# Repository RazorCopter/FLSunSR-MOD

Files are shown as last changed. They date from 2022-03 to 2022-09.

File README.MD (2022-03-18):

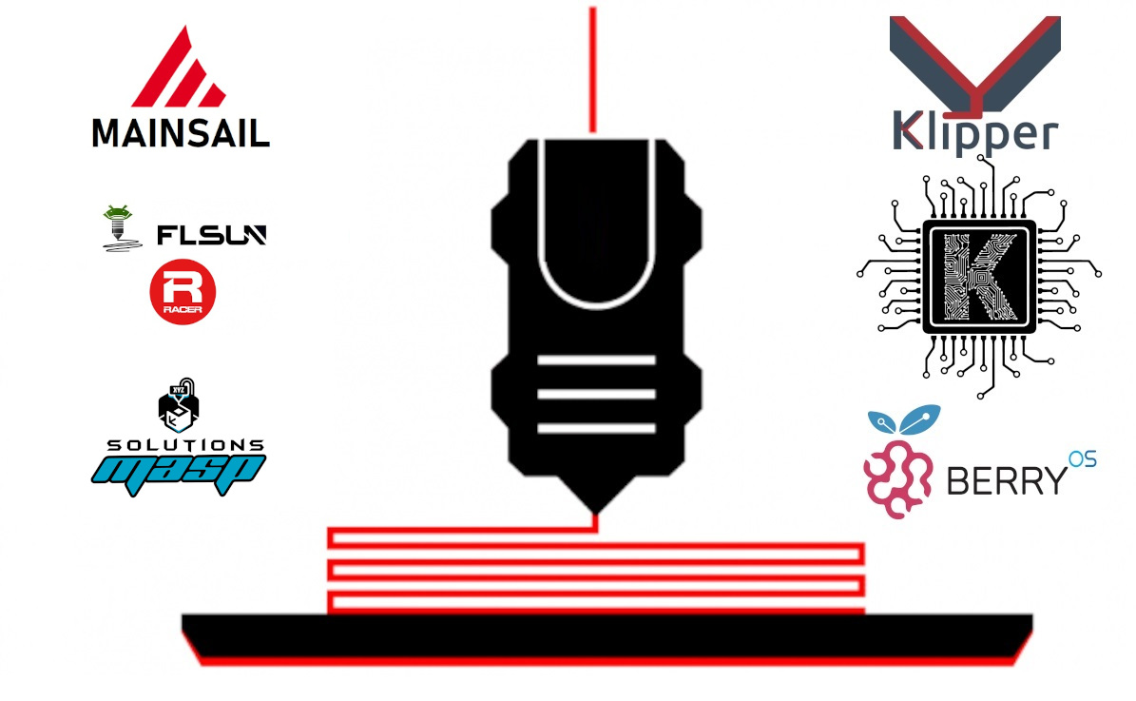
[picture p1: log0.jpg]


# Klipper + MAINSAIL >> FLSUN_SR

################### HW MOD ####################
+ Raspberry Pi 3B+
+ MASP HEAT BREAK [CTCore®] + VOLCANO
+ 2X NOCTUA FAN
+ DUALDRIVE BONDTECH EXTRUDER
+ LED-STRIP IN TOWERS 2835 24V
+ DISPLAY IPS 4.3" TOUCH CAPACITIVE
+ HOUSING & FAN DUCT REDESIGNED
+ CAM FULLHD

################### SW MOD #####################
- Klipper v0.10.x
- MainSail  v2.1.2
- Moonraker v0.7.1-x
- KlipperScreen v0.2.x

##################   Optional by KIAUH   #################

URL: https://github.com/th33xitus/kiauh

###############################################

# Install Klipper FLSUN SR:

 PREREQUISITES:
> Raspberry 
> Optional Display 
> Elettrical connection:
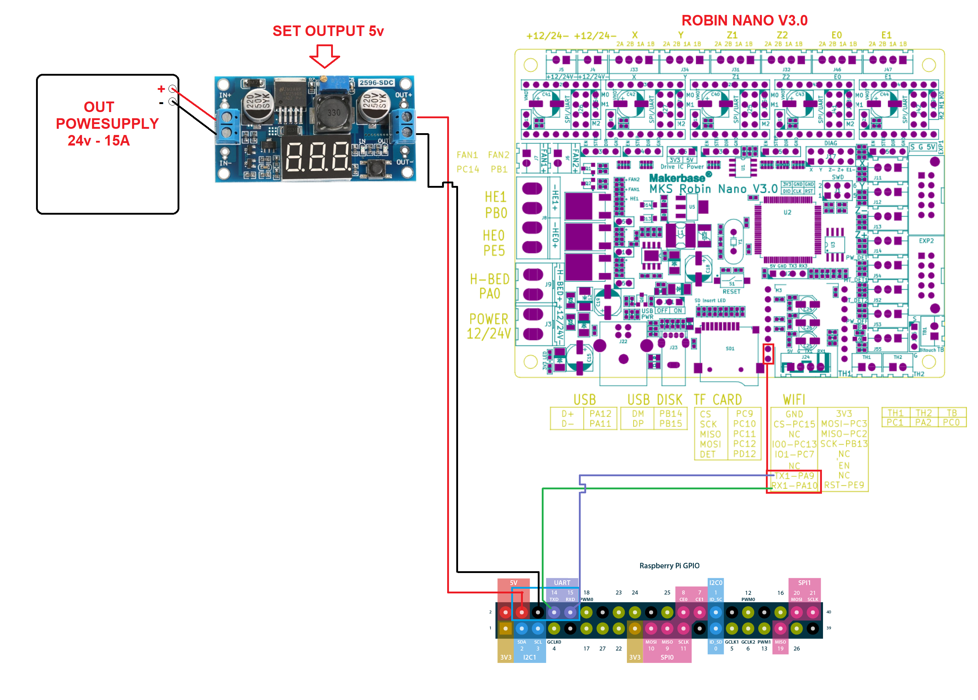
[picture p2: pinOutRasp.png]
PinLink


# STEP 1:
- Install Mainsail OS 
-     > https://github.com/mainsail-crew/MainsailOS/releases
-     > Guide: https://3dprintbeginner.com/how-to-install-mainsailos-on-raspberry-pi/

# STEP 2:
- SSH IP Raspberry (User/pwd > pi/raspberry)
- Launch commands:
```
cd klipper
make menuconfig
```
- ############################### SETTINGS ##############################
```
      > Micro-controller Architecture (STMicroelectronics STM32)  --->
      > Processor model (STM32F407)  --->
      > Bootloader offset (48KiB bootloader (MKS Robin Nano V3))  --->
      > Clock Reference (8 MHz crystal)  --->
      > Communication interface (Serial (on USART1 PA10/PA9))  --->
      > (250000) Baud rate for serial port
```
- Q > Yes
- Command: 
```
make
```
- copy generate file: /home/pi/klipper/out/klipper.bin in new SDCARD and rename in: Robin_nano_v3 (you can find it among the files here]

# STEP 3:
- Insert sdcard in the nano robin and wait and power-on SR
- Restart SR

# STEP 4:
- Open mainsail from browser
- leftmenu > Machine > edit printer.cfg :
```
[mcu]
serial: /dev/ttyAMA0
restart_method: command
baud: 250000
```
  
# NOTE:
- Serial port check: open ssh raspberry e launch command: 
```
ls /dev/ttyAMA*
```

//==========================================================================
//==========================================================================
//==========================================================================

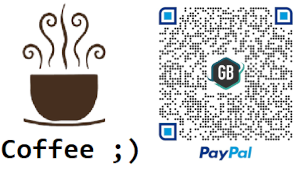
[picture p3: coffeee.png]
coffeee


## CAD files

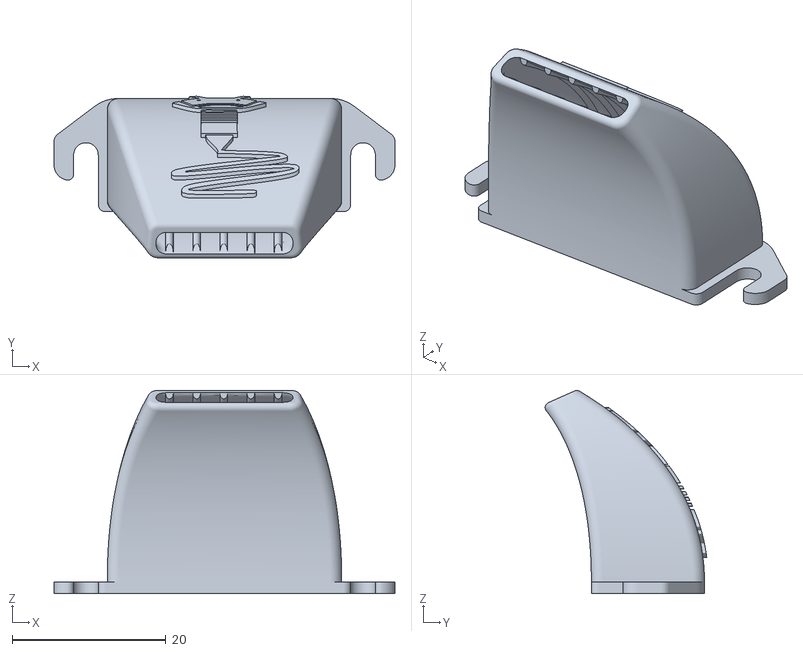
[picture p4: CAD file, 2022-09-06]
STL SR/FLSUN SR Fan_Duct V3 Fast Mount with logo.stl
44.3 x 21.0 x 26.4

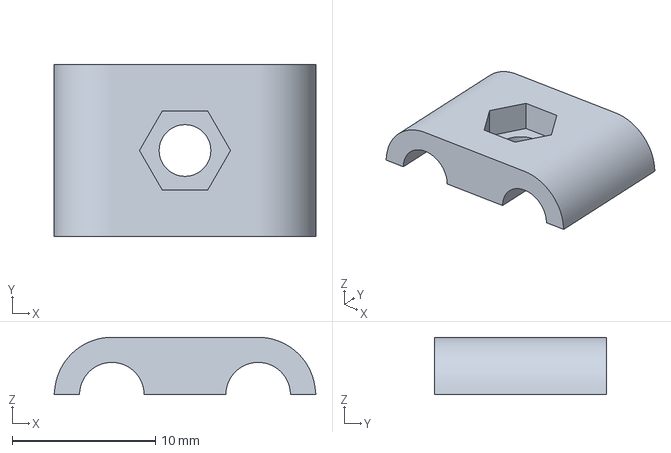
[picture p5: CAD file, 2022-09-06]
STL SR/Support ADXL/sr-adxl-a.3mf
18.3 x 12.0 x 4.00 mm

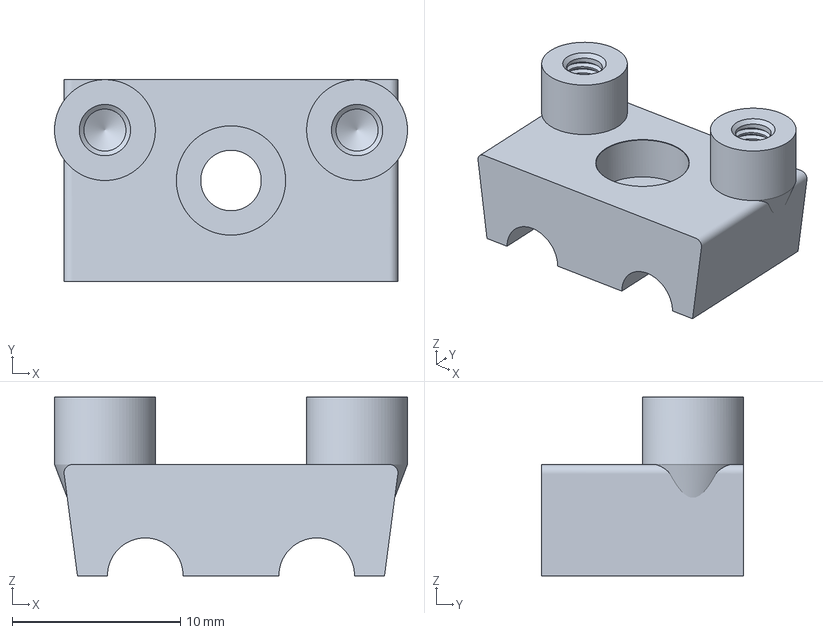
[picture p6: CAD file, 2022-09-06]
STL SR/Support ADXL/sr-adxl-b.3mf
21.0 x 12.0 x 10.6 mm

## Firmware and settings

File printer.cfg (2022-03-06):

#KLIPPER COMMANDS: ENDSTOP_PHASE_CALIBRATE stepper=stepper_(LETTER) REMOVE BRACKETS. PROBE_CALIBRATE DELTA_CALIBRATE (DO THIS AT PRINTING TEMP) SET FANS 40 PERCENT THEN PID_CALIBRATE HEATER=extruder TARGET=245
# SAVE_CONFG , PID_CALIBRATE HEATER=heater_bed TARGET=80, SAVE_CONFIG. your done. adjust slicer / retract accordingly. 
# OR RUN THE CALIBRATE MACRO MAKE SURE THE PROBE IS ON FOR ALL BED RELATED CALIBRATION INCLUDING Z OFFSET. NOTE FOR THE PAPER METHOD USE THE DEFAULTS IN KLIIPPER DOCS FOR #DELTA CALIBRATE / KINEMATICS REGARDING IT. 
# If the calibrate macro is used. run probe_calibrate first (aka zoffset) then run the macro. calibrate may need to be run 2x.
# Initially its safer to set the zoffset in fluidd/mainsaill a bit higher eg .2mmm or so then lower to 0 while printing a flat square or circle. This is a good safety measure to avoid a slight collison. 
############################################################################################################################################################
##MACHINE ABSOLUTE LIMITS / MOTION CONTROL / CONNECTED MCUS#/  ADD A # TO DISABLE MCU IF YOU DON'T HAVE ADXL OR PACKAGES INSTALLED 
############################################################################################################################################################
[include macroSR.cfg]

[printer]
kinematics: delta
max_velocity: 300
max_accel: 3000  #3000-9000-20000 after tuning with adxl / inputshaper stay to lower values otherwise starting out. eg 6000 note marlin default is 2800 this may work better on some printers or filament types 
max_accel_to_decel:999999 #I AM HALF MAX SET ACC BY DEFAULT. I CONTROL ZIG ZAG MOVEMENTS AND ADJUST VELOCITY BASED ON DIMENSIONS AND SMOOTH THINGS OUT. SET TO MAX WOULD BE SIMILAR TO MARLIN BEHAVIOR ADXL WIL COVER ROUGH MOVEMENTS. INCREASING MAX ACC IS USUALLY THE BETTER SOLUTION. 
max_z_accel: 3000 # this default should be fine / max acceration for z moves. (It may help to bump this up or down a bit depending on desired noise / zhop height. 
minimum_z_position: -25 #Once you find your z offset it is suggested to return this to 0 to avoid potentially crashing a nozzle for whatever reason. z offset shouldn't change unless the hotend has been adjusted. most things are flow related. 
square_corner_velocity: 5 # This can depend on desired speed to quality. higher values 15 -20 generally work fine. Left as a safe default. acc / corner velcoity can be adjusted with slicer controls macros handle this. i use a default of 15-30 or dynamic values. 
#delta_radius: 151.62 
print_radius: 133

[idle_timeout]
#gcode:
timeout: 300 #TIME BEFORE PRINTER TURNS OFF HEATERS AND STEPPERS MAX IDLE TIME 5MINS 
############################################################################################################################################################
#MAINBOARD / ACCELEROMETER SECTION.
############################################################################################################################################################
[mcu]
serial: /dev/ttyAMA0
restart_method: command
baud: 250000
#serial: /dev/serial/by-id/usb-Klipper_stm32f407xx_260044001651303239383037-if00 # Run ls /dev/serial/by-id/* on your Raspberry Pi to get YOUR serial or it wont connect

#[mcu rpi]  #https://www.klipper3d.org/Measuring_Resonances.html GO HERE TO INSTALL ACCELEROMETERS DO NOT TRUST THE PICTURE FOR WIRING THE GPIO LABEL ISN'T IN THE RIGHT SPOT.
#serial: /tmp/klipper_host_mcu  

#[adxl345] #TURN ME OFN BY REMOVING THE #. IF YOU HAVE ONE. EXAMPLE [ADXL345] IS NOW ON REMOVE# TO ENABLE OR ADD # TO ENABLE FEATURES.  DO NOT CONFUSE THIS WITH MARLIN.  
#cs_pin: rpi:None 

#[resonance_tester] # ENABLE  THIS  IF YOU HAVE ADXL ACCELEROMETER . USE MANUAL METHOD IF YOU DONT INSTEAD. https://www.klipper3d.org/Resonance_Compensation.html
#accel_chip: adxl345
#max_smoothing: 0.20  # an example
#min_freq: 5
#max_freq: 120
#accel_per_hz: 25
#probe_points: 
     #0,0,5
     
#[input_shaper]   #PLACE HOLDER VALUES 
#shaper_type_x = zv
#shaper_freq_x = 0
#shaper_type_y = zv
#shaper_freq_y = 0
############################################################################################################################################################
# A (X-Stepper) Configuration  ENABLE ARM LENGTH , ANGLE , POSITION ENDSTOP. FOR THE FIRST TIME EVER. DELTA CALIBRATE WILL ADJUST THIS AND SAVE AT THE BOTTOM. 
############################################################################################################################################################
[stepper_a] # X
step_pin: PE3
dir_pin: PE2
enable_pin: !PE4
microsteps: 128 # TMC ARE MENT TO BE SET TO THE HIGHEST VALUE THE MCU CAN SUPPORT THIS DOES NOT WORK THE SAME AS OLDER DRIVERS.  DON'T TOUCH ROTATION DISTANCE JUST THIS IF YOU WANT TO CHANGE IT (KLIPPER WILL CALCULATE STEPPING AUTOMATICALLY) 
rotation_distance: 40 #NEVER ADJUST THESE VALUES. ADJUSTING THIS WILL NOT SOLVE DIMENSION ISSUES. HORIZONTAL OFFSET / FLOW. OTHERWISE BELTS, OR RAILS MAY NOT BE MOVING RIGHT FOR THIS TO HAPPEN.  
full_steps_per_rotation: 200 #CHANGE THIS TO 400 FOR 0.9 DEGREE STEPPERS AGAIN KLIIPPER WILL CALCULATE THE NEW VALUES AUTOMATICALLY 
endstop_pin: ^PA15 
homing_speed: 60 # This is left a bit slow for initial start up safty once everything is setup up 70-90 are reasonable. (note the sr has optical endstops it can home fast This value needs to be changed on a,b,c steppers)
homing_retract_dist: 5.0
homing_retract_speed:10
#arm_length: 315 #note turning this one applys for b and c as well. 
#position_endstop: 336.5 #note turning this one applys for b and c as well. 

[tmc2209 stepper_a]
uart_pin: PD5
interpolate: false
run_current: 1.100 #THIS IS RMS CURRENT NOT VREF FOR TMC. based on oem flsun data sheets.  
stealthchop_threshold:999999 #this forces always silent (STEALTHCHOP). due to the stepper location turning this off will result in amplifed noise due to the case acoustics SPECIFIC TO THE SR. 
############################################################################################################################################################
# B (Y-Stepper)  Configuration 
############################################################################################################################################################
[stepper_b] # Y
step_pin: PE0
dir_pin: PB9
enable_pin: !PE1
microsteps: 128
rotation_distance: 40
full_steps_per_rotation: 200
endstop_pin: ^PD2 
homing_speed: 60
homing_retract_dist: 5.0
homing_retract_speed: 10 

[tmc2209 stepper_b]
uart_pin: PD7
interpolate: false
run_current: 1.100
stealthchop_threshold:999999
############################################################################################################################################################
# C (Z-Stepper)  Configuration
############################################################################################################################################################
[stepper_c] # Z
step_pin: PB5
dir_pin: PB4
enable_pin: !PB8
microsteps: 128
rotation_distance: 40
full_steps_per_rotation: 200
endstop_pin: ^PC4 
homing_speed: 60
homing_retract_dist: 5.0
homing_retract_speed: 10
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

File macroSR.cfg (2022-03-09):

############################################################################################################################################################
#MACROS 
############################################################################################################################################################
[gcode_macro BED_MESH] #or rename Bed_mesh 
description: Mash mapping 
gcode:
  M117 MESH MAPPING 
  G28
  bed_tilt_calibrate #Or replace with bed_mesh_calibrate 
############################################################################################################################################################
[gcode_macro CALIBRAZIONE_DELTA] #dont forget to put on the probe. 
description: Procedura calibrazione Delta #extended delta calibrate in klipper docs should also be done at some point. 
gcode:
  M117 Calibrazione DELTA 
  G28
  G91
  G1 Z-50 F1500
  G90
  G28
  G91
  G1 Z-50 F1500
  G90
  G28
  G91
  G1 Z-50 F1500
  G90
  G28
  G91
  G1 Z-50 F1500
  G90
  G28
  G91
  G1 Z-50 F1500
  G90
  G28
  ENDSTOP_PHASE_CALIBRATE stepper=stepper_a
  ENDSTOP_PHASE_CALIBRATE stepper=stepper_b
  ENDSTOP_PHASE_CALIBRATE stepper=stepper_c
  DELTA_CALIBRATE
  DELTA_CALIBRATE
  DELTA_CALIBRATE
  DELTA_CALIBRATE
  DELTA_CALIBRATE 
  G28
  SAVE_CONFIG 
 ############################################################################################################################################################
#IF ENABLED KEEP WALL ACCELERATION THE SAME WITH PRESSURE ADVANCE THIS ALSO APPLIES TO M205. DO NOT FORGET KLIPPER DOES NOT USE JERK THE VALUES ARE NOT THE SAME AND SCALE WITH ACC. 
#THIS IS BOTH FOR COMPATABILITY WITH CERTAIN SLICERS AND FOR DYNAMIC ACC 
[gcode_macro M204]
rename_existing: M204.1
gcode:
  {% set f = params.F|default(0.85)|float %} # DEFAULT 0.85 = 85 PERCENT OF SET ACCELERATION VIA SLICER FOR ACCEL TO DECEL 
  {% if 'S' in params %}
  {% set s = params.S|float %}
  SET_VELOCITY_LIMIT ACCEL={s} ACCEL_TO_DECEL={ s * f }
  {% else %}
  {% if 'P' in params %}
  {% set p = params.P|float %}
  {% if 'T' in params %}
  {% set t = params.T|float %}
  {% if p < t %}
  SET_VELOCITY_LIMIT ACCEL={p} ACCEL_TO_DECEL={ p * f }
  {% else %}
  SET_VELOCITY_LIMIT ACCEL={t} ACCEL_TO_DECEL={ t * f }
  {% endif %}
  {% else %}
  SET_VELOCITY_LIMIT ACCEL={p} ACCEL_TO_DECEL={ p * f }
  {% endif %}
  {% elif 'T' in params %}
  {% set t = params.T|float %}
  SET_VELOCITY_LIMIT ACCEL={t} ACCEL_TO_DECEL={ t * f }
  {% endif %}
  {% endif %}
############################################################################################################################################################
[gcode_macro M205]
gcode:
  {% if 'X' in params %}
  SET_VELOCITY_LIMIT SQUARE_CORNER_VELOCITY={params.X}
  {% elif 'Y' in params %}
  SET_VELOCITY_LIMIT SQUARE_CORNER_VELOCITY={params.Y}
  {% endif %}
############################################################################################################################################################
[gcode_macro PID_BED]
description: Calibrazione PID Piatto TEMP: 110
gcode:
   PID_CALIBRATE HEATER=heater_bed TARGET=110
############################################################################################################################################################
[gcode_macro PID_HOTEND]
description: Calibrazione PID HotEND TEMP: 220
gcode:
   G28
   G91
   M106 S128
   G1 Z-50 F1500
   PID_CALIBRATE HEATER=extruder TARGET=220
   G28
   SAVE_CONFIG  
############################################################################################################################################################
[gcode_macro G29]
gcode:
  {% set t = params.T|default(0)|float %}
  {% if printer.idle_timeout.state == "Printing" %}
  {action_respond_info("This command cannot be used while printing")}
  {% elif printer.toolhead.homed_axes != "xyz" %}
  {action_respond_info("Please home XYZ first")}
  {% else %}
  SAVE_GCODE_STATE NAME=G29_state
  G90
  G1 Z10 F240
  {% if t > 30.0 %}
   M190 S{t}
  {% endif %}
  BED_MESH_CALIBRATE
  {% if 'S' in params %}
  M140 S{params.S}
  {% endif %}
  G90
  G1 Z20 F240
  G1 X0 Y0 F6000
  RESTORE_GCODE_STATE NAME=G29_state MOVE=0
  {% endif %}
############################################################################################################################################################
[gcode_macro PAUSE]
description: Pausa in stampa
rename_existing: PAUSE_BASE
# change this if you need more or less extrusion
variable_extrude: 1.0
gcode:
  M117 Stampa in PAUSA 
  ##### read E from pause macro #####
  {% set E = printer["gcode_macro PAUSE"].extrude|float %}
  ##### set park positon for x and y #####
  # default is your max posion from your printer.cfg
  {% set x_park = printer.toolhead.axis_maximum.x|float - 5.0 %}
  {% set y_park = printer.toolhead.axis_maximum.y|float - 5.0 %}
  ##### calculate save lift position #####
  {% set max_z = printer.toolhead.axis_maximum.z|float %}
  {% set act_z = printer.toolhead.position.z|float %}
  {% if act_z < (max_z - 2.0) %}
      {% set z_safe = 2.0 %}
  {% else %}
      {% set z_safe = max_z - act_z %}
  {% endif %}
############################################################################################################################################################
  PAUSE_BASE
  G91
  {% if printer.extruder.can_extrude|lower == 'true' %}
    G1 E-{E} F2100
  {% else %}
    {action_respond_info("Extruder not hot enough")}
  {% endif %}
  {% if "xyz" in printer.toolhead.homed_axes %}
    G1 Z{z_safe} F900
    G90
    G1 X{x_park} Y{y_park} F6000
  {% else %}
    {action_respond_info("Printer not homed")}
  {% endif %} 
############################################################################################################################################################
[gcode_macro CANCEL_PRINT]
description: Annula stampa in corso..
rename_existing: CANCEL_PRINT_BASE
gcode:
  G28
  TURN_OFF_HEATERS
  CANCEL_PRINT_BASE
  M117 Stampa ANNULLATA! 
############################################################################################################################################################
[gcode_macro UTL_UNLOAD_FILAMENTO]
description: Scarico filmanto..
gcode:
  SAVE_GCODE_STATE NAME=unload_state
  G91                                     # Relative positioning
  M117 Heating...
  M109 S{params.TEMP|default(220, true)}  # Heat up hotend to provided temp or 220 as default as that should work OK with most filaments.
  M117 Unloading filament...
  G0 E50 F400                             # Purge
  G0 E-50 F1500                           # Quick Retract 
  G0 E-475 F500                           # Unload the rest of the filament
  M117 Filamento RIMOSSO!
  RESTORE_GCODE_STATE NAME=unload_state
############################################################################################################################################################
[gcode_macro RESUME]
description: Ripresa stampa in corso
rename_existing: RESUME_BASE
gcode:
  ##### read E from pause macro #####
  {% set E = printer["gcode_macro PAUSE"].extrude|float %}
  #### get VELOCITY parameter if specified ####
  {% if 'VELOCITY' in params|upper %}
    {% set get_params = ('VELOCITY=' + params.VELOCITY)  %}
  {%else %}
    {% set get_params = "" %}
  {% endif %}
  ##### end of definitions #####
  {% if printer.extruder.can_extrude|lower == 'true' %}
    G91
    G1 E{E} F2100
  {% else %}
    {action_respond_info("Extruder not hot enough")}
  {% endif %}  
  RESUME_BASE {get_params}
############################################################################################################################################################
[gcode_macro UTL_LOAD_FILAMENTO]
description: Caricamento Filamento
gcode:
  SAVE_GCODE_STATE NAME=load_state
  G91                                     #Relative positioning
  M117 Riscaldamento...
  M109 S{params.TEMP|default(220, true)}  #Heat up hotend to provided temp or 220 as default as that should work OK with most filaments.
  M117 Caricamento filamento in corso...
  G0 E475 F1000                           # Load the filament into the hotend area.
  G4 P1000
  G0 E50 F200                             # Purge
  M400
  TURN_OFF_HEATERS
  M117 Filamento caricato!
  RESTORE_GCODE_STATE NAME=load_state
############################################################################################################################################################
[gcode_macro UTL_ARCO_PULIZIA]
description: Pulizia con ARCO
gcode:
    M117 Pulizia con ARCO!
    G92 E0
    G1 X-130 Y0 Z0.2 F1000; move to arc start
    G3 X0 Y-130 I130 Z0.2 E40 F200 ; lay arc stripe 90deg
    M106 S255
    G1 Z10 F25
    M106 S0
    G1 X0 Y0 F3000
    M106 S0
    G92 E0
############################################################################################################################################################
[gcode_macro EXT_CALIBRAZIONE]
description: Calibrazione estrusore 10cm
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

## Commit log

2022-03-06 Add files via upload
    Klipper on MCU (UART Mode)
2022-03-06 Add files via upload
    My personal file config
    [printer.cfg]
2022-03-09 Macro for klipper
    add [include macroSR.cfg] in printer.cfg
    [macroSR.cfg]
2022-09-06 Create STL
